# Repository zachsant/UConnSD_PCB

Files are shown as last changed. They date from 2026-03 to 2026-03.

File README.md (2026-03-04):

# UUV Power Sensor Hub PCB

This project is a 4-layer PCB designed as part of the University of Connecticut Senior Design program. Our team, ECE 2622, was assigned this project by the Naval Undersea Warfare Center (NUWC). The board provides power distribution and sensor interfacing for a variable ballasting system used in unmanned underwater vehicles (UUVs). The PCB is designed to connect to an off board Arduino Uno R3 running a PID loop to control pumps and solenoids which manage the inlet and outlet flow to adjust the depth of the vehicle.

## Schematic Overview
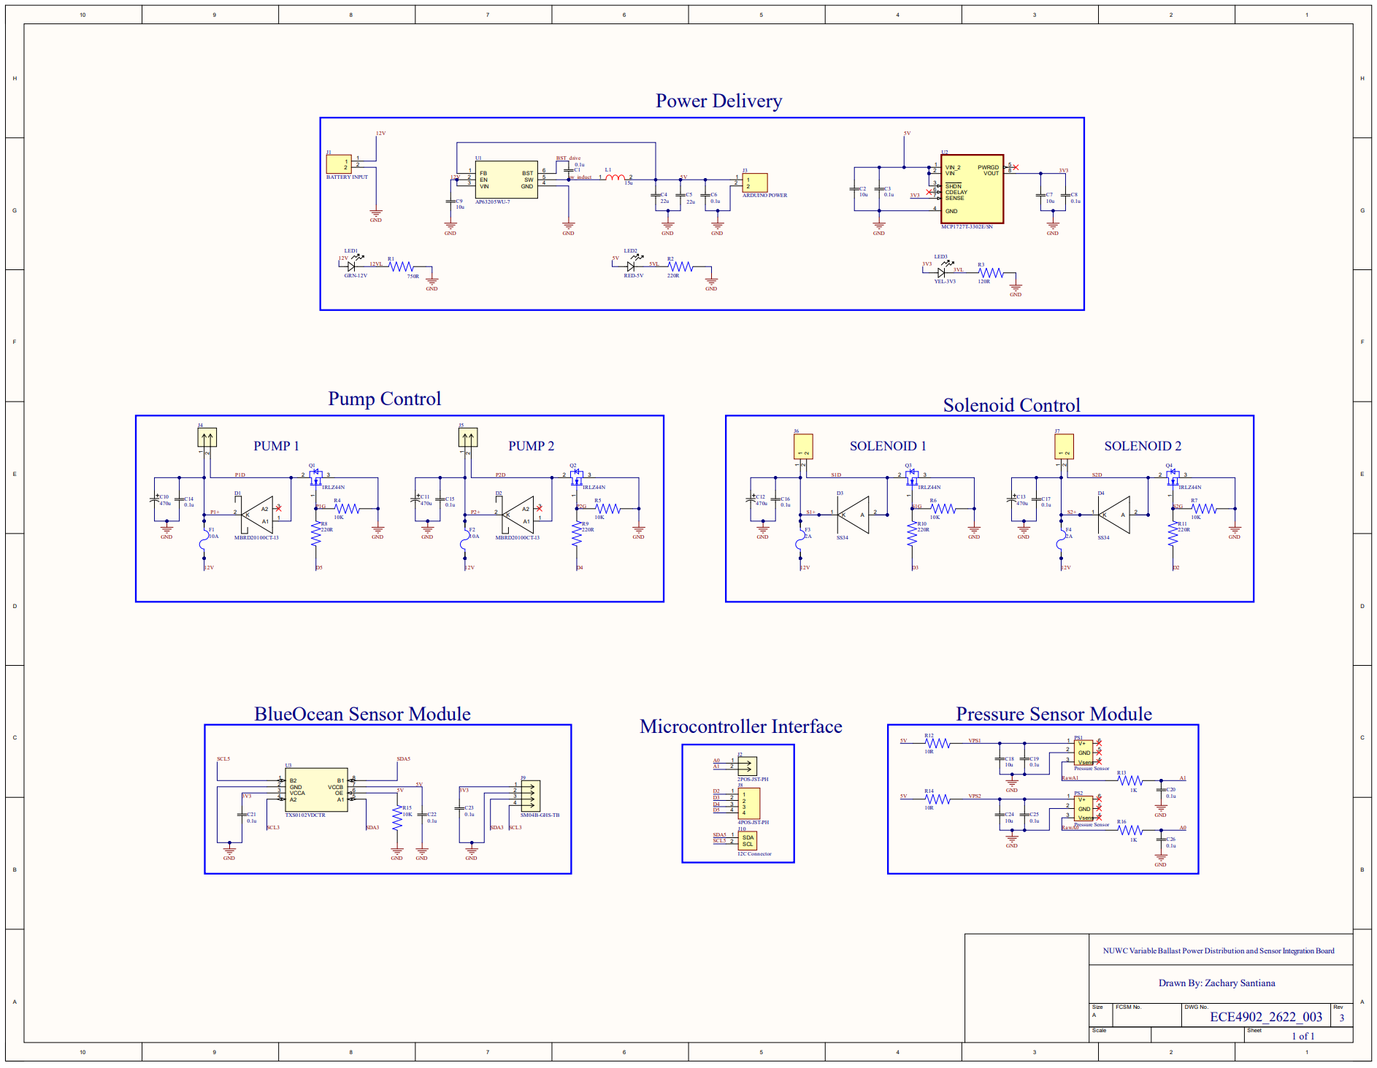
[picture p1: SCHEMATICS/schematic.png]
Schematic Overview

12V input is dropped to 5V with buck converter. An inductor of 6.8uH was selected due to the low current requirements of the digital components. A linear regulator is used to drop the 5V to 3V3, as the BlueOcean sensor communicates over I2C at 3V3. Proper bulk, decoupling and filtering capacitors have been added where necessary based on datasheet guidelines and recommended circuit calculations.

## Board Rendering
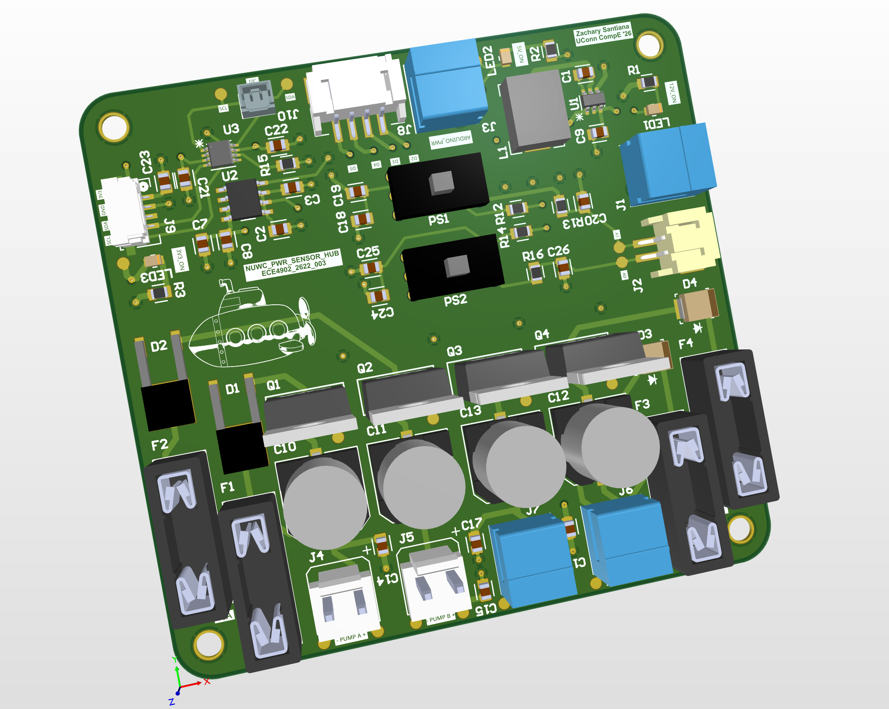
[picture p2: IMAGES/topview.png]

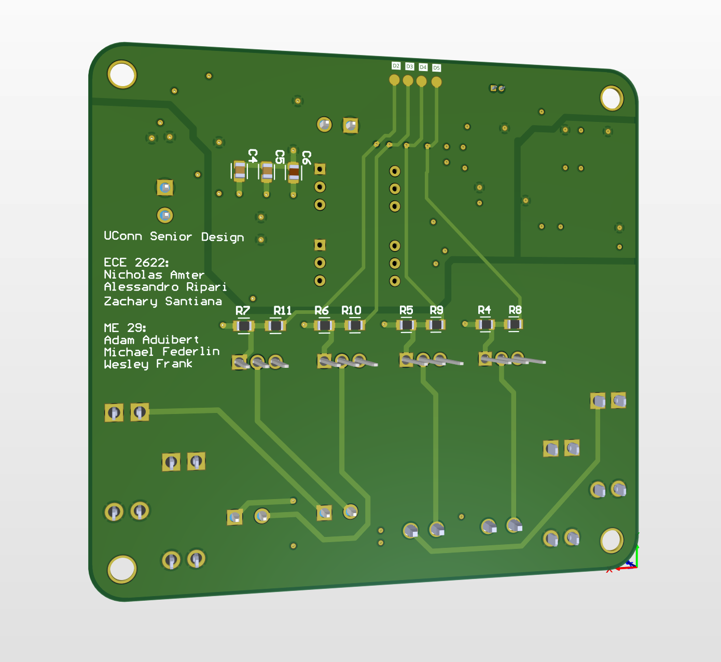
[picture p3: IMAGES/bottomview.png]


## Characteristics
The PCB is 3.2"x3" and 0805 components were used wherever possible to balance hand solderability and space constraints. All connectors are labeled with pinout information and are non-reversible.
- JST-PH 2 POS -> Analog signal from Pressure Sensors
- JST-PH 4 POS -> Digital input signal from Arduino
- Molex PicoBlade 2 POS -> I2C cable (3V3 and GND already connected)
- Overcurrent protection with fuses on each high current output and one main switch fuse
- High side MOSFET driver with flyback protection
- Terminal block headers, JST-PH, JST-GH, and Molex PicoBlade connectors used

## Layer Stack
1. Top Copper -> Signals and components
2. GND Plane -> No splits, signal reference voltage
3. PWR Plane -> Split 12V, 5V, 3V3 sections
4. Bottom Copper -> Signals and components

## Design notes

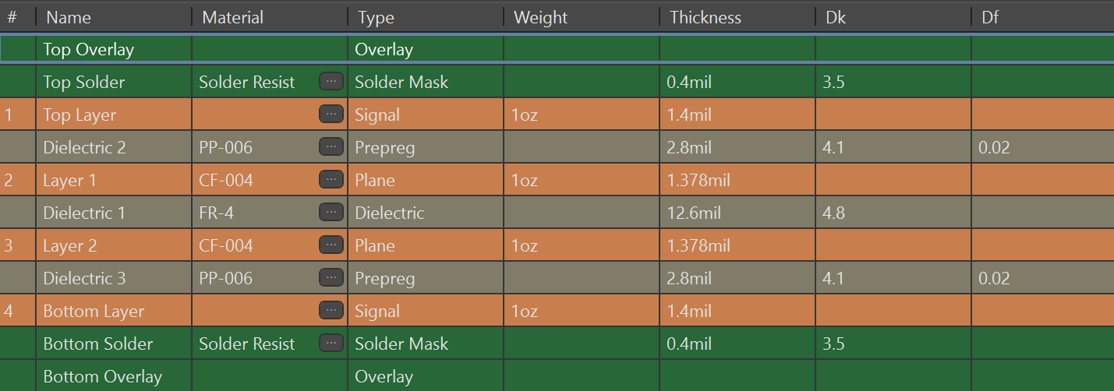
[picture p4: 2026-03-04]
IMAGES/layerstackup.png

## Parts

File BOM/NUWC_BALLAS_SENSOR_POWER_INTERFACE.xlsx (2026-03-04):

Comment | Description | Designator | Footprint | LibRef | Quantity
C0805C104K3RACTU | Capacitor;Ceramic;Cap;.0.1uF;Tol 10%;SMT;Vol-Rtg 25V;X7R;Tape and Reel | KEMET C0805C104K3RACTU | C1, C3, C6, C8, C14, C15, C16, C17, C19, C20, C21, C22, C23, C25, C26 | CAP_0805_KEMET | C0805C104K3RACTU | 15
C0805C106K3PACTU | Capacitor;Ceramic;Cap;.10uF;Tol 10%;SMT;Vol-Rtg 25V;X5R;Tape and Reel | KEMET C0805C106K3PACTU | C2, C7, C9, C18, C24 | CAP_0805_KEMET | C0805C106K3PACTU | 5
CL21A226MAYNNNE | Multilayer Ceramic Capacitors MLCC - SMD/SMT 22uF+/-20% 25V X5R 2012 | C4, C5 | CAP_0805_SAMSUNG | CL21A226MAYNNNE | 2
UWT1E471MNL1GS | 470u | C10, C11, C12, C13 | PCAP_10x10-ELECT_NCA | UWT1E471MNL1GS_1 | 4
MBRD20100CT-13 | DIODE ARR SCHOT 100V 10A TO2523 Diodes Incorporated | D1, D2 | MBRD20100CT_SHOT_DIODE | MBRD20100CT-13 | 2
SS34 | Description | D3, D4 | SHOTT_DIODE | SS34 | 2
10A | THM 2 in 1 Auto Blade Holder | F1, F2 | FUSE_3557-2 | 3557-2 | 2
2A | THM 2 in 1 Auto Blade Holder | F3, F4 | FUSE_3557-2 | 3557-2 | 2
BATTERY INPUT | 2~24 Poles, Pluggable,Receptacle, Horizontal, 3.81 Pitch, Terminal Block Connector | J1, J6, J7 | CUI_TBP02R1-381-02BE | TBP02R1-381-02BE | 3
2POS-JST-PH |  | J2 | JST_S2B-PH-SM4-TB | JST_PH_2POS_SMD_RA | 1
ARDUINO POWER | 2~24 Poles, Pluggable,Receptacle, Horizontal, 3.81 Pitch, Terminal Block Connector | J3 | CUI_TBP02R1-381-02BE | TBP02R1-381-02BE | 1
26607020 | KK 396 Solid Right-Angle Header, Friction Lock, with Snap-in Plastic Peg PCB Lock, 2 Circuits, Tin (Sn) Plating | J4, J5 | CONN_SD-42892-001_M450_02_MOL | 26607020 | 2
4POS-JST-PH | Connector Header Surface Mount, Right Angle 4 position 0.079 (2.00mm) | J8 | JST_S4B-PH-SM4-TB | S4B-PH-SM4-TB | 1
SM04B-GHS-TB | Description | J9 | CONN_SM04B-GHS-TB_JST | SM04B-GHS-TB | 1
I2C Connector | Connector Header Through Hole 2 position 0.049 (1.25mm) | J10 | MOLEX_530470210 | I2C Connector | 1
15u |  | L1 | inductor | Inductor | 1
GRN-12V | GREEN DIFF LED | LED1 | LED_LGR971-KN-1_OSR | LGR971-KN-1 | 1
RED-5V | RED DIFF LED | LED2 | LED_LGR971-KN-1_OSR | LS R976-NR-1-0-20-R18 | 1
YEL-3V3 | YEL DIFF LED | LED3 | LED_LGR971-KN-1_OSR | LY R976-PS-36-0-20-R18 | 1
Pressure Sensor |  | PS1, PS2 | PCBComponent_1 | Pressure Sensor | 2
IRLZ44N | OptiMOS 3 Power-Transistor, VDS 100V | Q1, Q2, Q3, Q4 | IFX-PG-TO220-3-904-1 | IRLZ44N | 4
CRCW08051K00FKEA | Resistor,Thick Film,1 Kilohms,0.125 W,1%,SMT,0805,TCR 37 ppm/DegC,Cut Tape | Vishay Dale CRCW08051K00FKEA | R1, R13, R16 | RESC2012X50N | CRCW08051K00FKEA | 3
CRCW0805560RFKEA | Resistor,Thick Film,560 Ohms,0.125 W,1%,SMT,0805,TCR 37 ppm/DegC,Cut Tape | Vishay Dale CRCW0805560RFKEA | R2 | RESC2012X50N | CRCW0805560RFKEA | 1
CRCW0805120RFKEA | Resistor,Thick Film,120 Ohms,0.125 W,1%,SMT,0805,TCR 37 ppm/DegC,Cut Tape | Vishay Dale CRCW0805120RFKEA | R3 | RESC2012X50N | CRCW0805120RFKEA | 1
CRCW080510K0FKEA | Resistor,Thick Film,10 Kilohms,0.125 W,1%,SMT,0805,TCR 37 ppm/DegC,Cut Tape | Vishay Dale CRCW080510K0FKEA | R4, R5, R6, R7, R15 | RESC2012X50N | CRCW080510K0FKEA | 5
CRCW0805220RFKEA | Resistor,Thick Film,220 Ohms,0.125 W,1%,SMT,0805,TCR 37 ppm/DegC,Cut Tape | Vishay Dale CRCW0805220RFKEA | R8, R9, R10, R11 | RESC2012X50N | CRCW0805220RFKEA | 4
CRCW080510R0FKEA | Resistor,Thick Film, 10 Ohms,0.125 W,1%,SMT,0805,TCR 37 ppm/DegC,Cut Tape | Vishay Dale CRCW08051K00FKEA | R12, R14 | RESC2012X50N | CRCW080510R0FKEA | 2
AP63205WU-7 | Description | U1 | SOIC_05WU-7_DIO | AP63205WU-7 | 1
MCP1727T-3302E/SN | 1.5A CMOS LDO, Vout=3.3V, Extended Temp Range | Microchip Technology Inc. MCP1727T-3302E/SN | U2 | SOIC127P490X175-8N | MCP1727T-3302E/SN | 1
TXS0102VDCTR | Two-bit bidirectional level shifter for open-drain and push-pull applications 8-SSOP -40 to 85 | U3 | SSOP8_DCT_TEX | TXS0102VDCTR | 1

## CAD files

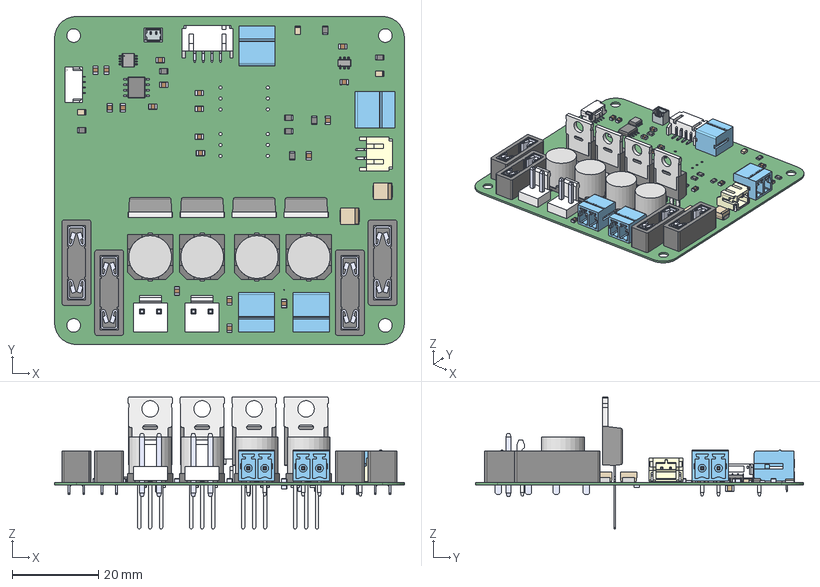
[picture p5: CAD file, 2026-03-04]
3D/BallastControlBoard_4902-003.step
81.3 x 76.2 x 30.6 mm
BxP-VH_2 x 2
pin x 8
PG-TO220-3-904_Z8B00198139_V06_3D x 4
SMxB-GHS-TB_04
SxB-PH-SM4-TB white_4

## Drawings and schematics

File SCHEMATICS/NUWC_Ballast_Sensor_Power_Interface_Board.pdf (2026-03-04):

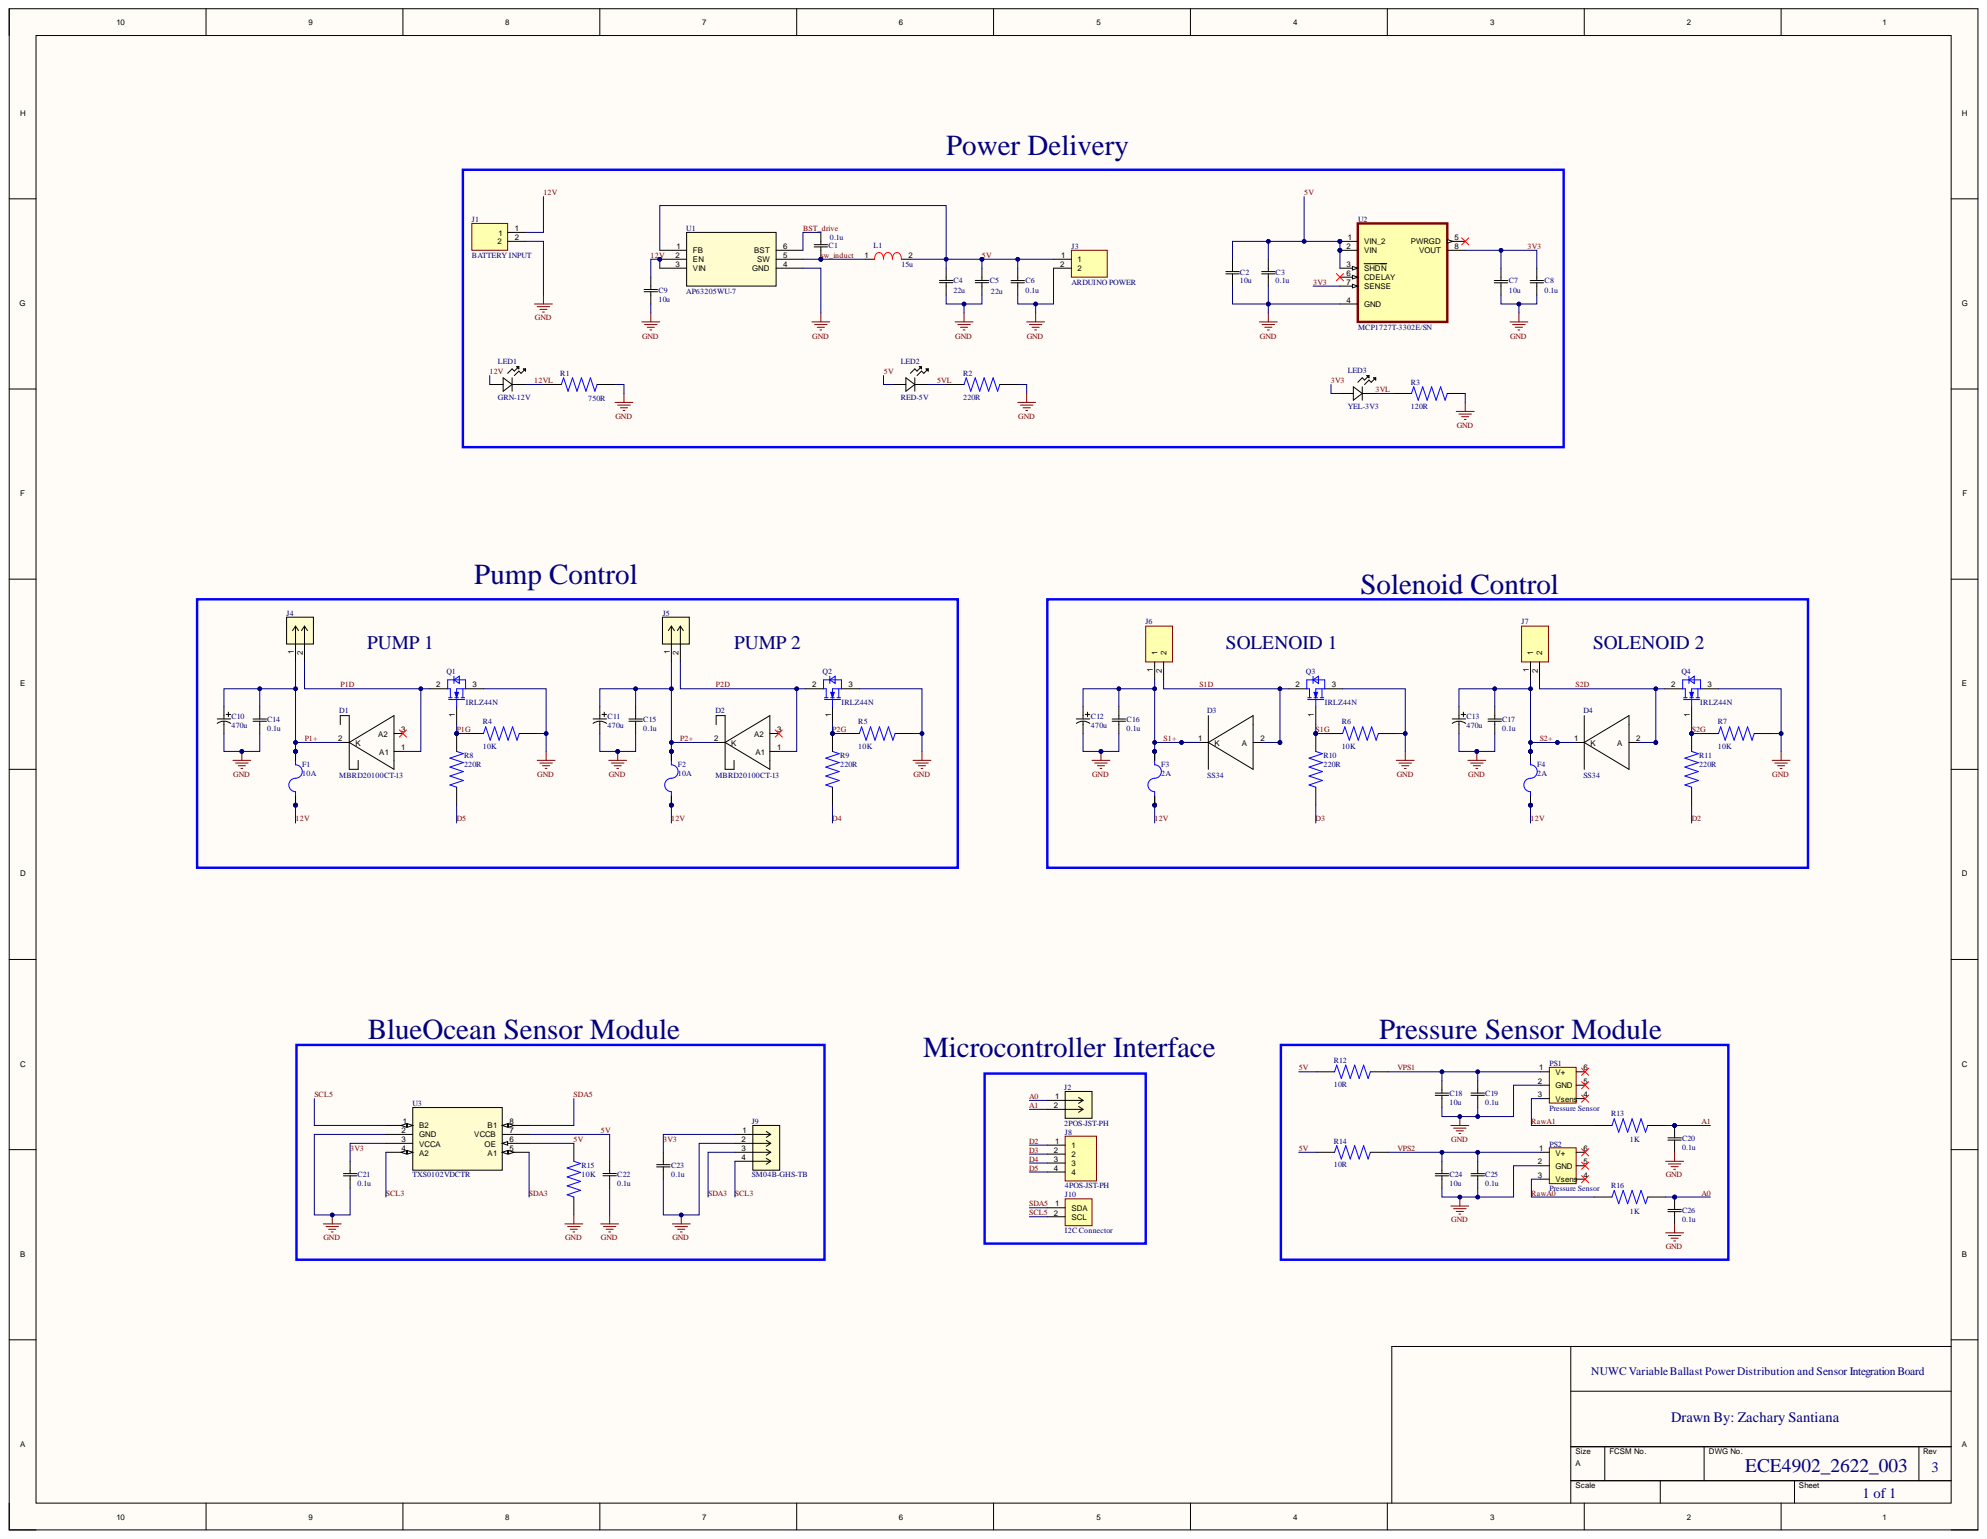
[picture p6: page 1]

VIN 2

LED2 5V | 2 2

GND 4

NUWC VariableBallast Power Distribution and Sensor Integration Board

Drawn By: Zachary Santiana

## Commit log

2026-03-04 Initial PCB Project Structure commit
    [BallastControlBoard_4902-003.step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]
2026-03-04 Added schematic png
